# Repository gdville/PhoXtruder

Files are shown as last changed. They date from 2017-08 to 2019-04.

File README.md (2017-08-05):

# PhoXtruder
Open Source design for extruding Magnesia-Phosphate cement.

## What is Magnesium Phosphate Cement (MPC)?
Magnesium phosphate ceramics (MPC) have been in use since ancient times and have recently been making something of a comeback as “green cement”. Premixed powder formulations are commercially available as Grancrete, Ceramicrete, Bindan Monopatch, and other products. Compared to Ordinary Portland Cement (OPC), it can cure at relatively cold temperatures, almost to freezing, and cure in minutes, resulting in a stronger and more hermetic material, with less thermal expansion. It also takes far less energy to produce, making it the "green" alternative.

## Why an extruder?
One thing inhibiting the adoption of this material is the fast cure time - the slurry pot life is unforgiving and large volumes can lose strength due to water cavitation caused by the fast exothermic reactions. This has caused problems in the construction industry with manually poured foundation methods. However, these characteristics could become much more advantageous when done with additive printing techniques, particularly considering that the MPC chemistry utilizes covalent bonds that adhere rather than merely encapsulating (as OPC does). Progressively applying thin layers of fast curing MPC offers to provide a potentially strong and versatile construction method.  

## Why open source?
For one, that is where the talent is in the 3D printing world.  For another thing, this is a technology that needs to be shared to help people now in need of housing.  Finally, it is my dream to really save humanity and eventually use this technology to autonomously construct habitats on Mars, where phosphates are 5 times as abundant as on Earth. 

## Where do I start?
Check out the wiki or dive into the design tree.

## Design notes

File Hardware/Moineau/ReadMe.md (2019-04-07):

The Moineau pump is a controlled method of pumping slurries. Moineau pumps are comprised primarily of a rotor and a stator. The rotor is usually driven eccentrically while the stator is held in place.

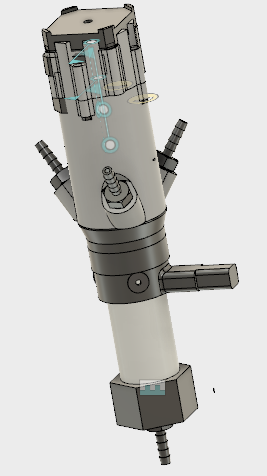
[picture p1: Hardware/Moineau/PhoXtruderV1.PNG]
Moineau Assembly


In addition to the rotor and stator, this design includes:
* manifold - house the gears and provide inlets for the slurries to enter and mix
* planetary gear set - eccentrically drive the rotor
* motor - stepper motor drives the gears (might be better to use brushless DC motor appropriately geared down to provide high torque)
* nozzle - shapes the extrusion

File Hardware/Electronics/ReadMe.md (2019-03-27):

# Electronics 

This system is designed to be controlled with RAMPS/MEGA electronics modified to run at 18-20Vdc. 
The reason for this is that 
* The intent is to eventually power the system with standard power tool (rechargeable) lithium batteries, which are typically either 18V or 20V.
* Higher voltage provides more power to the motors. 

Note that by driving the electronics at higher voltage, it is imperative that heat sinks and fans are used to cool the motor drivers and (possibly) the motors themselves.

You will need the following components:
* 1ea Power supply capable of at least 18-20Vdc and 7A
* 1ea MEGA2560
* 1ea RAMPS cape with motor drivers
* 1ea NEMA17 stepper motor with 5:1 planetary gear drive for the moineau pump

In the near term, this extruder system is intended to be used with existing 3D printer designs.  However, it may be advisable to replace NEMA17 motors with NEMA23 steppers.

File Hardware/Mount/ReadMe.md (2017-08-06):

# Mounts

This was originally designed to go on a DoBot arm.  That is currently the only adapter designed.  An adapter for RepRap Prusa i2 is coming soon. Would greatly value any contributions toward a delta effector.

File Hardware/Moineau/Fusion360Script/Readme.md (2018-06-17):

Creates an epicyclic helical rotor and stator. The rotor will typically need a shaft added. The stator generated is actually the solid model of the stator cavity. As the stator is frequently molded out of silicone, this allows the user to use the generated model for creating the mold tool, as well as more latitude in creating the external stator geometry (from which the generated stator body can be cut via a boolean operation).

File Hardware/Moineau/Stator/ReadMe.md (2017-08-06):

# Stator
The stator body is made from silicone, and enclosed in 1" PVC, with PLA or ABS caps.

Included here is a model of the stator itself. However, to manufacture it in silicone you can do the following:
1. 3D print in ABS the mold insert and cap. If you want to remove the insert in one piece use a high amount of infill. Smooth both with acetone, and apply soap film or other mold release agent (DO NOT use a silicone based mold release as it will only enhance adhesion of the silicone mold material).
2. Cut a length of 1" PVC (schedule 40), and insert into the base of the stator mold insert. Insert 1/8" drill bits (3 total) into the holes near the top. Attach the cap with a wood screw to the top of the stator insert.
3. Mix and pack your [silicone material](https://rawmaterialsuppliers.com/product/magikmold-gt-1350/)  into the mold you've made. Fill to the top of the PVC.
4. After the silicone has set, unscrew the cap and remove. Remove the drill bits and then remove the insert body. The silicone stator should remain in the PVC which will be the housing for it.

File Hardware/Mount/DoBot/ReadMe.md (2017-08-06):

#  DoBot

This mount slips over the PVC stator housing.

Print in either PLA or ABS. It is intended to be used with M3 screws self tapped into the holes.

See the [MOBOTS repository](https://github.com/gdville/MOBOTS) for the current state of arm modifications (electronics and software).

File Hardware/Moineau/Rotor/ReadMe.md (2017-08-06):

The rotor needs to be a relatively rigid, hard material, with a strong shaft. This design is for a steel shaft and fiberglass epoxy (e.g. "Bondo") composite rotor.

It can be manufactured by doing the following:
1. Make an ABS print of the rotor (simplest is to print half lengthwise twice and glue the halves together). Use acetone to smooth and seal the surface so that it will not adhere to the silicone mold. A film of soap may also help for mold release (DO NOT use a silicone based mold release product, as it will only enhance adhesion to the silicone mold!).
2. Use silicone mold making epoxy to create a rotor mold. This mold can be the same material (something like Magikmold-GT-1350 used in making the stator. A toilet paper tube can be used to contain the mold while it cures. Insert you ABS rotor in the wet mold keeping it centered in the tube. Allow to cure. Remove the ABS rotor insert. 
3. Prepare a 5mm steel rod (a 7/16" lag bolt can be ground down for this purpose) as the shaft. Grind some flats and rough the surface to improve adhesion. Dry fit the shaft and mark the depth where it should leave the mold.
4. Mix the fiberglass and resin, adding hardener, then pack into mold, squeezing out any air bubbles (it's good to poke a small overflow hole at the bottom of the silicone mold to prevent air entrapment). 
5. Insert the shaft up to the depth mark you made. Cure the resin. Remove shaft from mold. Grind away any flash or burrs. 
6. The rotor surface can be further treated by applying a silicone spray sealant, to help reduce friction in the stator.

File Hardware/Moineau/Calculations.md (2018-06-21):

# Calculations

## Rotor
* 2Lobe cross section area 68.751mm^2 + 19.635 = 88.39 mm^2
* rotor pitch = 38mm per turn (360 degrees) = 0.1056 mm/deg 
* Dminor = Dmajor * (lobes - 1) / (lobes + 1)
* Dpitch = (Dmajor + Dminor) / 2 

## Stator
* Inner radius = 10mm
* Outer radius = 20mm
* 3Lobe Cross section area = pi*13.322^2-369.704 mm^2 = 187.85mm^2
 
## Cavity
* Cavity area = 187.85 - 88.39 = 99.46 mm^2
* Pump length = 20cm
* Pump volume = Cavity area * pump length = 12.6 cc

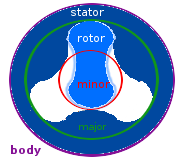
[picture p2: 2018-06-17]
Hardware/Moineau/Fusion360Script/Moineau.png

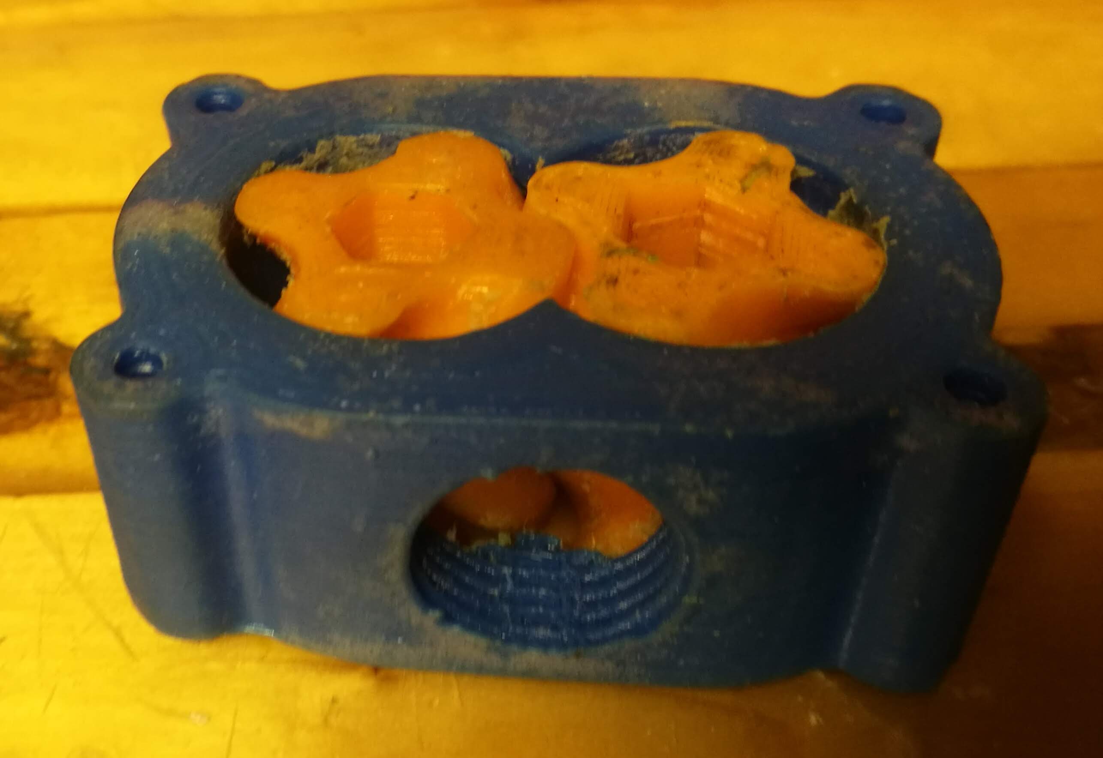
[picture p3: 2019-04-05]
Images/LobePump.jpg

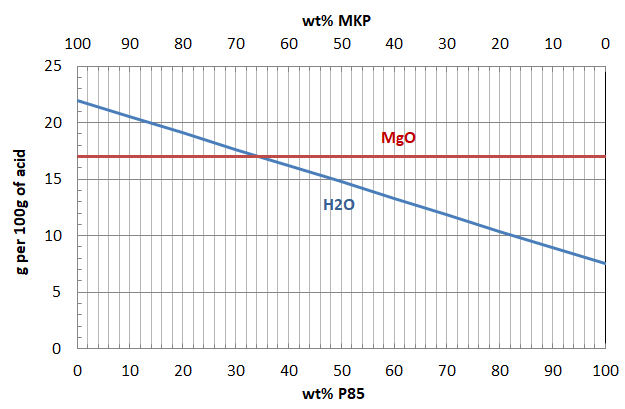
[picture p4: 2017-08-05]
Images/MPC_RecipeSpace.PNG

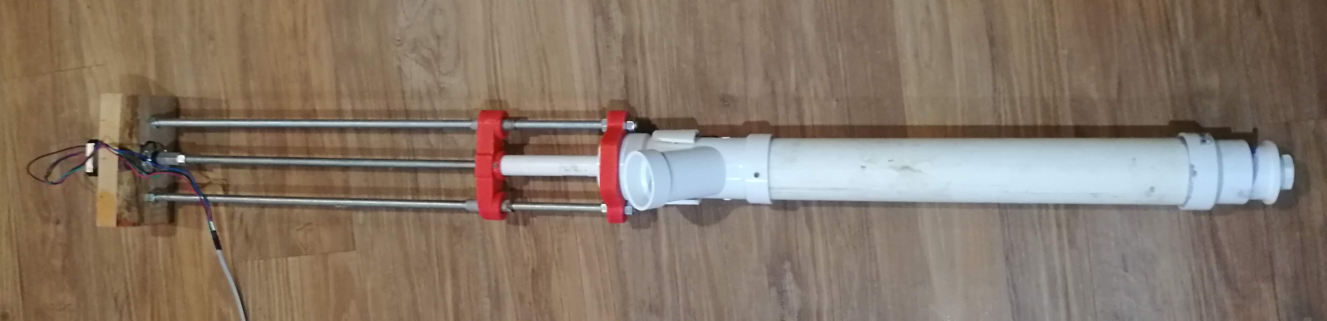
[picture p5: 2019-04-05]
Images/SyringePump.jpg

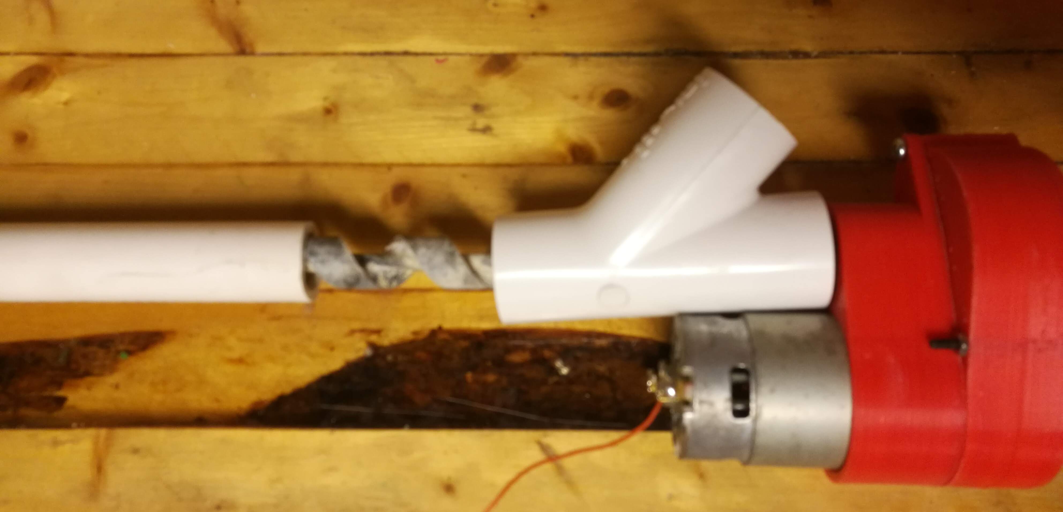
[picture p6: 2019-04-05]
Images/AugerPump.jpg

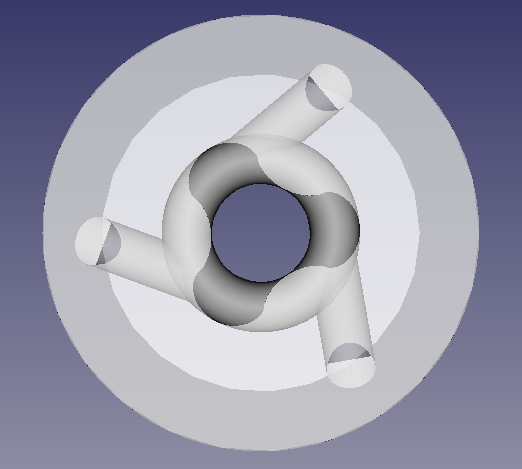
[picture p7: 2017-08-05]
Images/stator.PNG

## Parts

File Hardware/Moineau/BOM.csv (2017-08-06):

# NHA | Item | Description | Qty | UoM | Source | Model
0. | 0 | PhoXtruder Assembly | 1 | ea | Assemble | N/A
0. | 1 | Nozzle | 1 | ea | 3D printed | Nozzle.f3d
0. | 2 | 1/4IN NYLON BARBED TUBE FITTING | 4 | ea | McMaster-Carr 5372K121 | 1/4IN NYLON BARBED TUBE FITTING_5372K1211.stl
1. | 0 | Stator | 1 | ea | mold (see instructions) | Stator.f3d

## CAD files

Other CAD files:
Hardware/Mount/DoBot/DoBotEffector.f3d
